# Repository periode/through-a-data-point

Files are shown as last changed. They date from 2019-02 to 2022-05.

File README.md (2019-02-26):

# through-a-data-point
Code + doc for Data Through Design 2019

## HARDWARE

- 4x [Stepper Motor](https://www.sparkfun.com/products/10848)
- 4x [L293D Driver IC](https://www.engineersgarage.com/electronic-components/l293d-motor-driver-ic)
- 1x [Raspberry Pi Model 3B](https://www.raspberrypi.org/products/raspberry-pi-3-model-b/)
- 1x Power Supply DC 12V 0.6A
- 1x [Power Connector](https://ftaelectronics.com/image/cache/catalog/RG6%20Cable%20and%20Connectors/Cat6%20Connectors/2Pcs%20CCTV%20Camera%20UTP%20Power%20DC%20Plug%202.1mm%205.5mm%20Fema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)
- 1x MicroSD Card 16GB

## SETUP

### Get the latest code
- from the pi, run: `wget http://enframed.net/deeds/controller.py`

### Video
- following [this](https://scribles.net/customizing-boot-up-screen-on-raspberry-pi/)
- download the latest video by running `wget http://enframed.net/deeds/legal_landscape.mp4` or `wget http://enframed.net/deeds/legal_portrait.mp4`

### Wiring

The diagram for wiring a **single motor** can be found [here](https://github.com/periode/through-a-data-point/tree/master/resources/single_stepper_diagram.pdf).

Things to take into consideration:
- The power source is represented as 2x AA Batteries. It should instead be the 12V power supply, connected to the [power connector](https://ftaelectronics.com/image/cache/catalog/RG6%20Cable%20and%20Connectors/Cat6%20Connectors/2Pcs%20CCTV%20Camera%20UTP%20Power%20DC%20Plug%202.1mm%205.5mm%20Fema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).
- The wires coming out of the stepper motor are black and red. For clarity, I've connected them to wires that are the same as their actual color (red, green, yellow, blue).
  - This means that red and yellow go on one side of the IC, while green and blue should go on the other side.
  
 #### Tip
 
 Here's a shortcut to finding wire pairs for a bipolar (4 wire) motor. Spin your stepper motor with your fingers. Depending on the size / holding torque this could be easy or pretty hard. All you really want from this is to get a feel how the motor spins without any of the wires connected to each other. Now that you know how hard it is to spin with your fingers, connect 2 wires together, any two. Try to spin the motor again. If it feels the same then these are **NOT** connected to the same coil. Disconnect these wires. Connect one of the other wires to one of the first wire pairs you tried. Try to spin the motors again. This should be **much** harder. If so, you have found your wire pairs. Each pair goes on one side of the L293D.

## Programming

In order to set up the raspberry pi, you will need to **install** it, **find** it, **connect** to it and **execute** the sample program.

1. Download the [disk image](https://drive.google.com/open?id=1BWNo9bP_HmcmEQR-66aUi-tPA5VI7Kre) that we will flash on the SD card.
2. Download [Etcher](https://www.balena.io/etcher/).
3. Insert the SD card in your computer.
4. Open Etcher, select the image you just downloaded and the SD card you just inserted, and flash.
5. Insert the microSD card in the raspberry pi and connect it to a power source. A microUSB plugged in to a laptop is enough.
6. Once the raspberry pi is powered up, you should see a solid blinking LED.

### How to find your IP Address
7. On your computer, open the Command Prompt and type `ping raspberrypi`. The [output](http://j.tlns.be/wp-content/uploads/2015/02/step2_ping.png) should give you the IP address of the raspberry pi. **Make sure you are on the same WiFi network as the raspberry Pi**.
7. Install [Fing](https://play.google.com/store/apps/details?id=com.overlook.android.fing) and scan your wifi network to find connected devices.
7. Insert the SD Card into your computer. A `boot` disk should appear. Inside the boot partition, create a file called `wpa_supplicant.conf`, this is the file which connects automatically to WiFi networks. The file contents should look like [this](https://github.com/periode/through-a-data-point/blob/master/code/wpa_supplicant.conf) (make sure it's the correct ssid/pw for your own wifi!).
7. Plug in the raspberry pi directly to your router. Then open the command prompt and type `arp -a`. Your raspberry pi is the device that starts with the MAC address `b8:27:eb`.

### Connect and run the code
8. Download [Putty](https://www.chiark.greenend.org.uk/~sgtatham/putty/latest.html) (you probably want the 64bit MSI version).
9. Enter the IP address of the raspberry pi in the `Host Name (or IP address)` field, with `Port` set to 22 and click `Open`.
10. A command prompt should open. When asked to login as, enter `pi` and for password enter `raspberry`.
11. You are now connected to the raspberry pi. To execute the code to make the stepper motor turn, type `python stepper.py` and press `ENTER`. Follow the prompts on the screen to select the delays/numbers of rotations.

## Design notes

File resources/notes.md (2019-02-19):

## TODO
- play a video on the raspberry pin (using `subprocess.POpen()` and `omxplayer`)
- write logic for one cycle
- - motors reset (how? manual setup? there should be an ssh connection possible to go and set it up)
- - 0. pick a video
- - 1. the video plays
- - 2. motors go up at a certain number of steps **step number is fixed for all motors** but there is the problem that sometimes the motors don't actually go through all the steps when they are too fast with the shift register... so we will need trial and error to figure out what is a safe number of steps
- - 3. once the numbers have gone up all these steps, we stop the video
- - 4. the motors go down the previous number of steps.
- - 5. go to step 1.

## MOTOR NOTES

for the motors pierre has:
- blue and yellow
- red and green

same coil: same side of the l293d

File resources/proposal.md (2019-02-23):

### Short description of your proposed exhibition
Below, just a point is a light installation which reveals the sensual intersection between data points whose effects are unquantifiable because they’re unavailable and data points whose effects are only too quantifiable, but not searchable.

This installation wants to highlight the cause and effect relationship between property transactions —often happening unbeknownst to and to the detriment of inhabitants— and the amount of sunlight that these inhabitants are exposed to. On a very physical level, property transfer results directly in the construction of ever-higher rises, following a logic of most value extraction from the land, which in turn manifests itself through a net disappearance of sunlight for current tenants and neighbors upon completion of the construction work.

On the one side, then, data quantifying the amount of sunlight that urban zones are exposed to throughout the year is well documented, and visualized using current state-of-the-art technology from both specialized outlets (MAS - Municipal Arts Society), and broadsheet publications (NYT - New York Times); it is the very experience of seeing the light disappear that prevents readers and audience members to truly experience what it meant, not to live in shadows, but to see the light disappear.

On the other side, as the buildings rise, they obfuscate the original act of their creation —the financial exchange of mortgages— as they get buried deeper and deeper into the ACRIS database, supposedly open, yet hardly searchable, hardly findable, only remnants of deeds.

### Proposal submission
Through a data point, darkly consists in three main components. A projector, a set of moveable pieces articulated by DC motors and controlled by a Raspberry Pi, and a set of documents from the ACRIS database being projected. Placed right in front of the projector lens, the moveable pieces slowly rise to the pace at which a given set of buildings is expected to be completed within a neighborhood in New York City, gradually obstructing the light from the projector, casting their shadow on the projected documents, a set of mortgage transactions which have allowed that construction to happen in the first place. As the light gets obstructed from below, the impression is that of these legal documents disappearing. Once the automated, makeshift building silhouette has completely covered the light, the system resets and moves on to another lot, another mortgage, another construction.

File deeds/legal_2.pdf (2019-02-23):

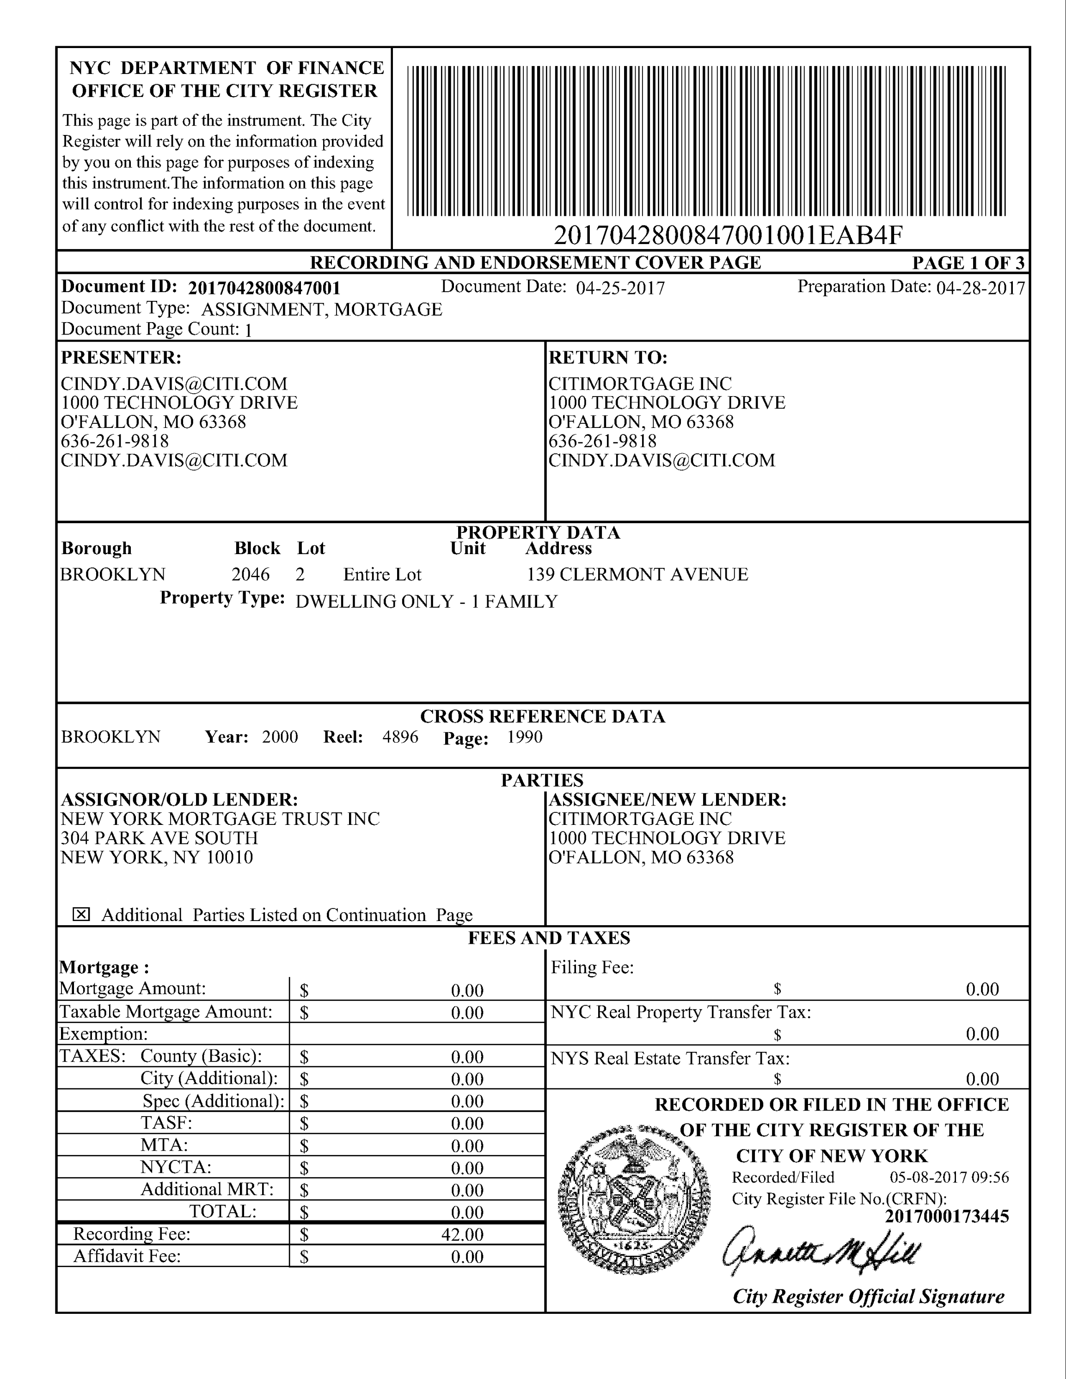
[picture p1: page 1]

Untitled Document | https://a836-acris.nyc.gov/DS/DocumentSearch/DocumentImag...
1 of 3 | 2/22/19, 6:17 PM

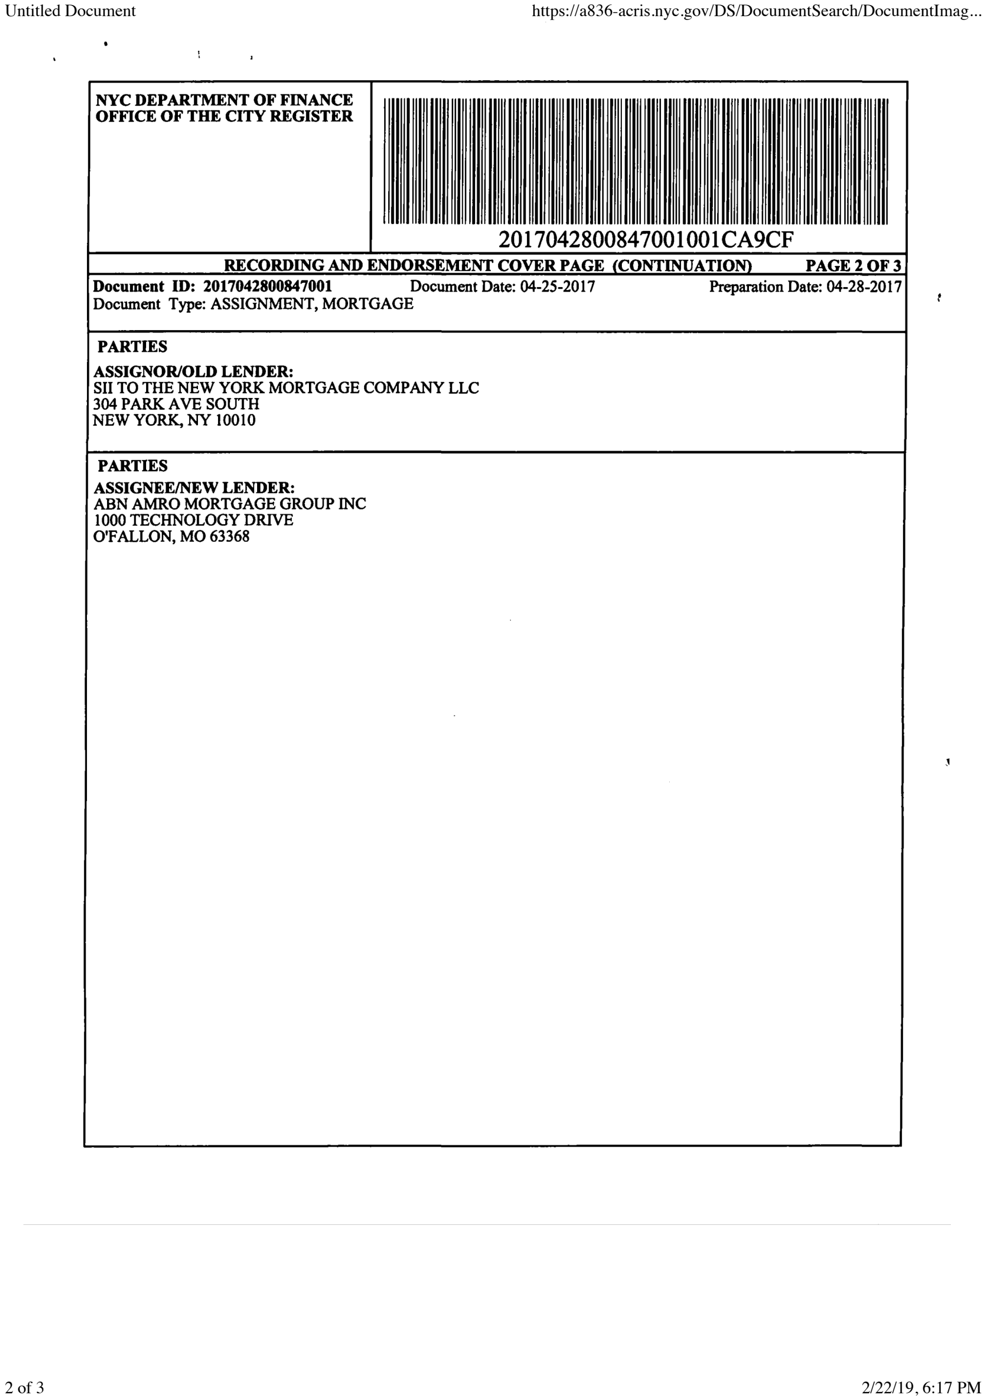
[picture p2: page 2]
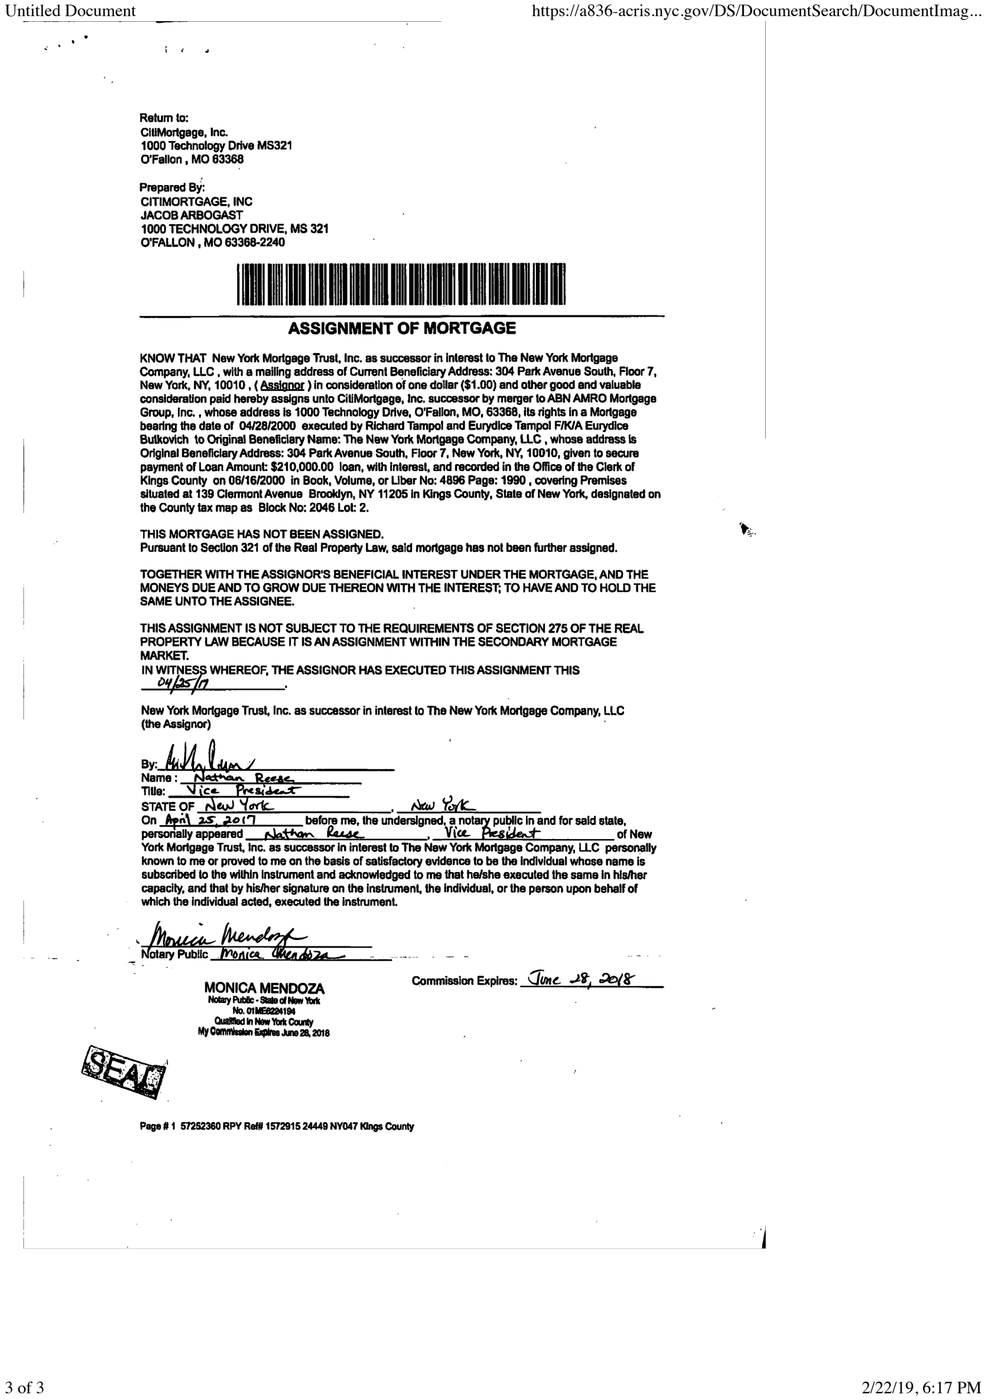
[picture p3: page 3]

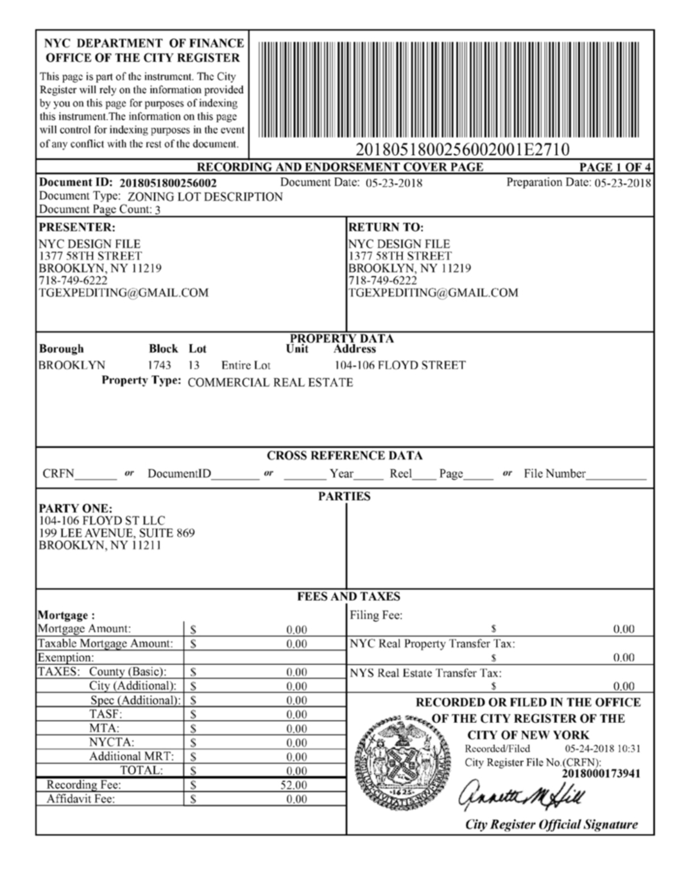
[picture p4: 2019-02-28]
deeds/img/legal_1-10.jpg

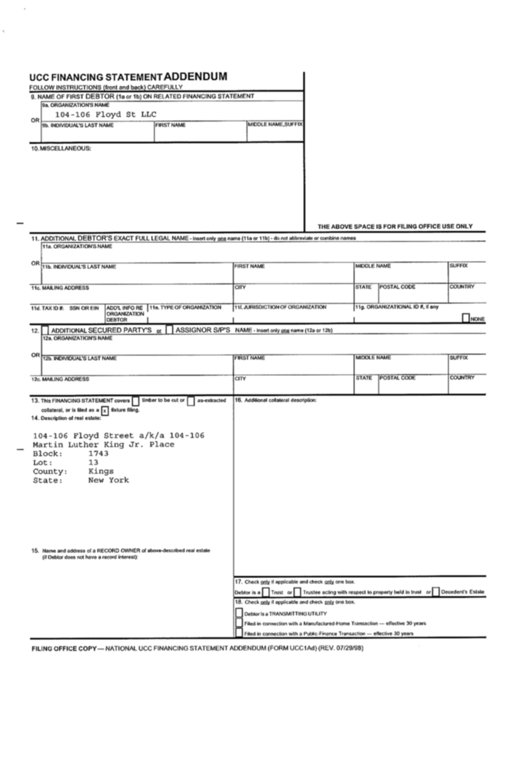
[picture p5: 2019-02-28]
deeds/img/legal_1-2.jpg

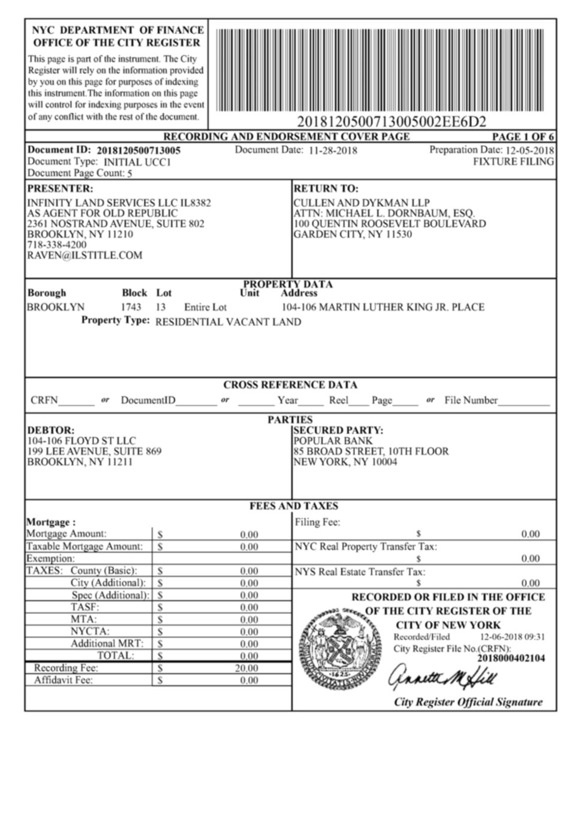
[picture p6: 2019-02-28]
deeds/img/legal_1-0.jpg

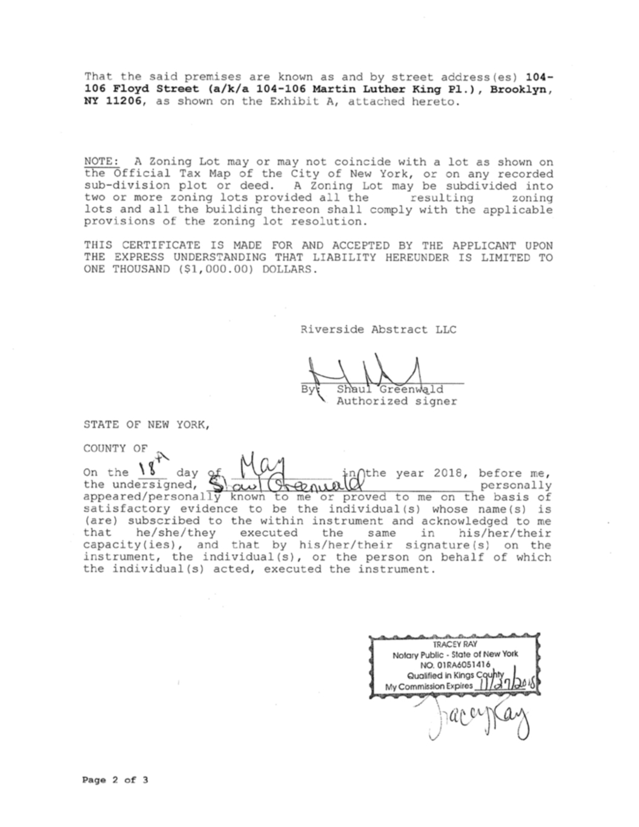
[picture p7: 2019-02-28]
deeds/img/legal_1-8.jpg

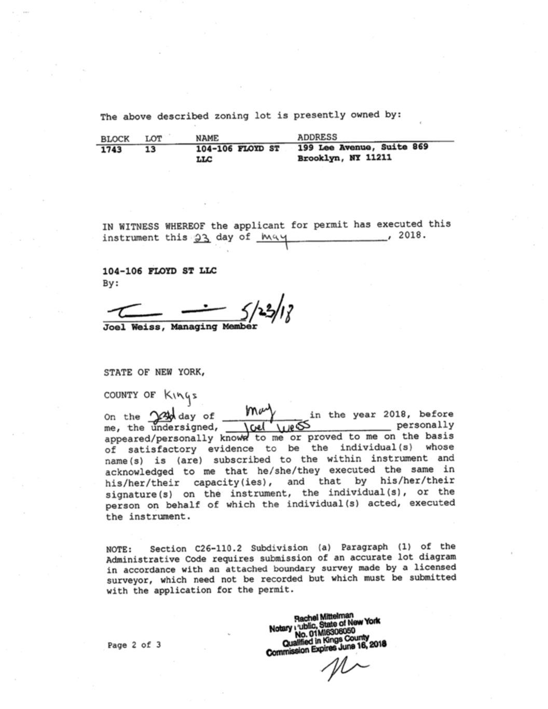
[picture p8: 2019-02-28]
deeds/img/legal_1-12.jpg

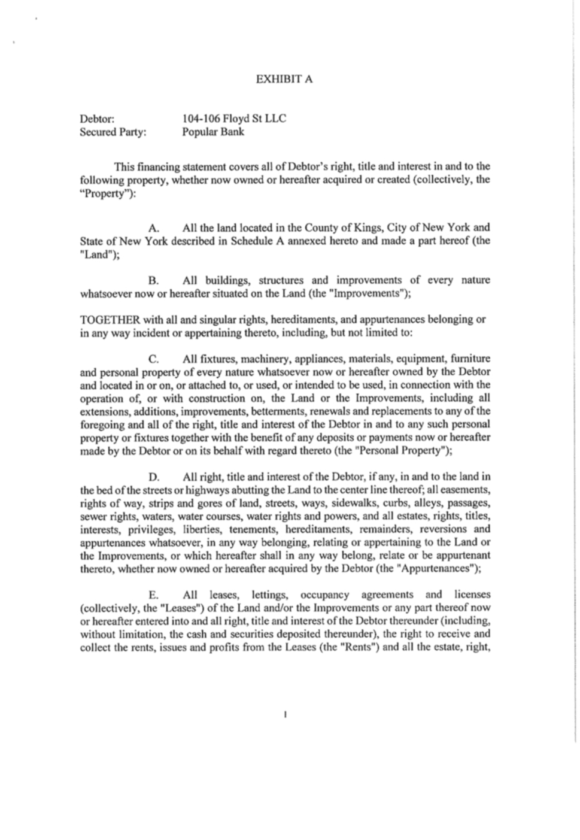
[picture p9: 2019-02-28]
deeds/img/legal_1-3.jpg

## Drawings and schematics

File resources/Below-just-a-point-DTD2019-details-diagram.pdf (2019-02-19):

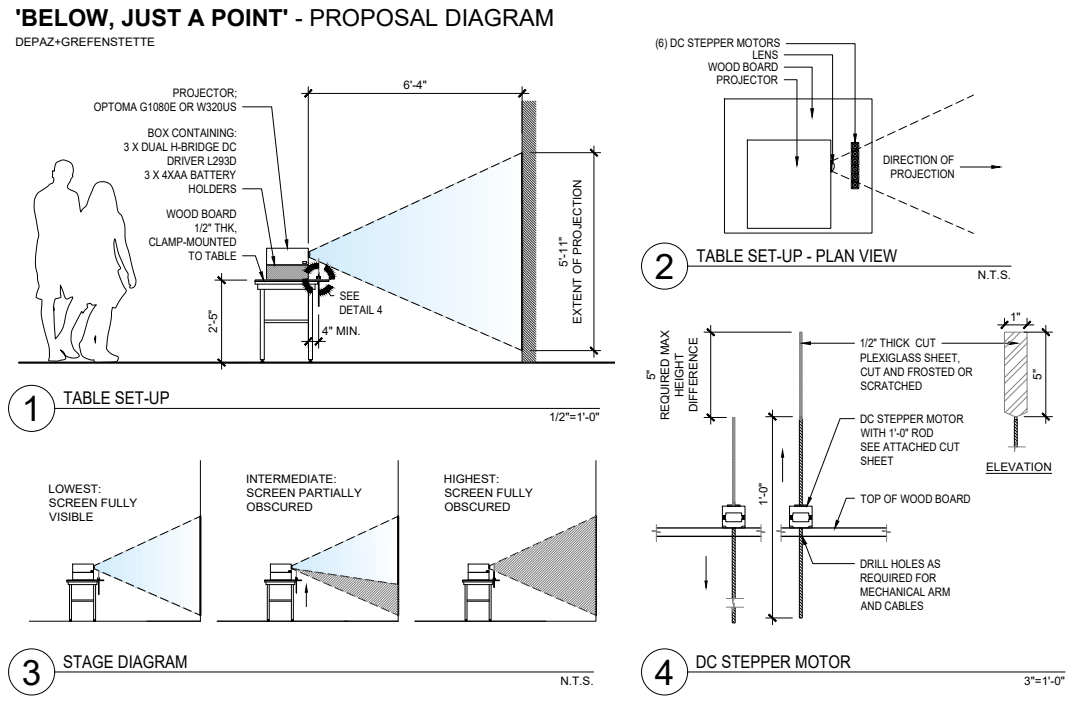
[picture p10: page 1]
REQUIRED MAX

5" ELEVATION TABLE SET-UP 1 1/2"=1'-0" TABLE SET-UP - PLAN VIEW 2 N.T.S. STAGE DIAGRAM 3 N.T.S. DC STEPPER MOTOR 4 3"=1'-0" 'BELOW, JUST A POINT' - PROPOSAL DIAGRAM DEPAZ+GREFENSTETTE

2'-5" LOWEST: SCREEN FULLY VISIBLE INTERMEDIATE: SCREEN PARTIALLY OBSCURED HIGHEST: SCREEN FULLY OBSCURED DIRECTION OF PROJECTION (6) DC STEPPER MOTORS LENS WOOD BOARD PROJECTOR

EXTENT OF PROJECTION 6'-4" 4" MIN. PROJECTOR; OPTOMA G1080E OR W320US BOX CONTAINING: 3 X DUAL H-BRIDGE DC DRIVER L293D 3 X 4XAA BATTERY HOLDERS WOOD BOARD 1/2" THK, CLAMP-MOUNTED TO TABLE SEE DETAIL 4

DIFFERENCE DC STEPPER MOTOR WITH 1'-0" ROD SEE ATTACHED CUT SHEET 1/2" THICK CUT PLEXIGLASS SHEET, CUT AND FROSTED OR SCRATCHED TOP OF WOOD BOARD DRILL HOLES AS REQUIRED FOR MECHANICAL ARM AND CABLES 1"

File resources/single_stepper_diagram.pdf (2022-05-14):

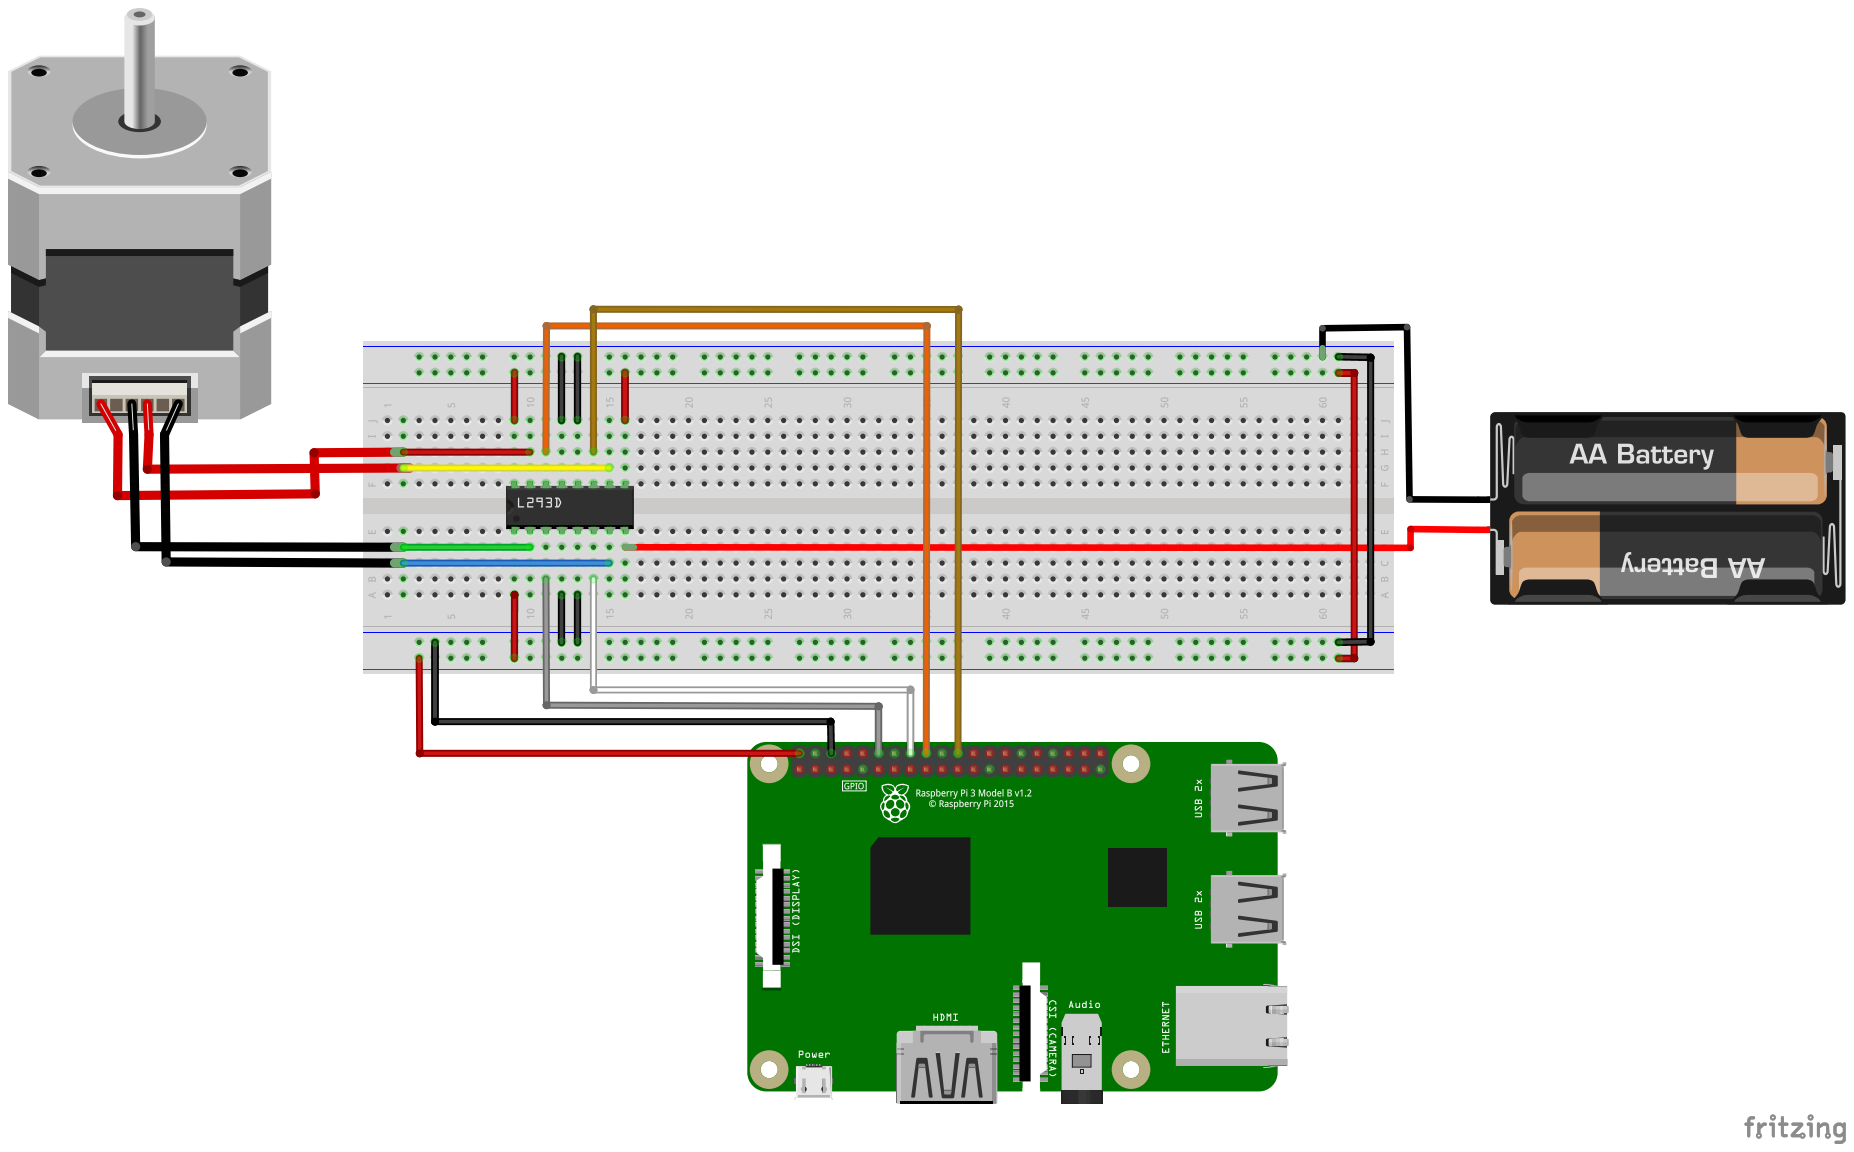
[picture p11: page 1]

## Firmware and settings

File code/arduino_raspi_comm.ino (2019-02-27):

bool isDone = false;
bool isGoingUp = true;

int startTime = 0;
int timer = 1000;

int currentSteps = 0;
int totalSteps = 120;

int delayUp = 25;
int delayDown = 5;

int motor1pinA = 2;
int motor1pinB = 4;
int motor1pinC = 3;
int motor1pinD = 5;

void setup() {

  pinMode(motor1pinA, OUTPUT);
  pinMode(motor1pinB, OUTPUT);
  pinMode(motor1pinC, OUTPUT);
  pinMode(motor1pinD, OUTPUT);
  
  Serial.begin(9600);
}

void loop() {
//  if(millis() - startTime > timer){
//      Serial.println(isDone);
//  
//      isDone = !isDone;
//      startTime = millis();
//  }

  // first we're going up, for up to X steps
  if(currentSteps < totalSteps && isGoingUp){
    up();  
    currentSteps++;
  }else{ //if we've reached the top
    if(isGoingUp){ //we send a signal to the pi
      Serial.println("reached top");
      isGoingUp = false;
    }
    
    down();
    currentSteps--;

    if(currentSteps == 0){ //if we've reached the bottom
      Serial.println("reached bottom");
      isGoingUp = true;
    }
    
  }
  

}

void up(){
  digitalWrite(motor1pinA, HIGH);
  digitalWrite(motor1pinB, LOW);
  digitalWrite(motor1pinC, LOW);
  digitalWrite(motor1pinD, LOW);
  delay(delayUp);
  digitalWrite(motor1pinA, LOW);
  digitalWrite(motor1pinB, HIGH);
  digitalWrite(motor1pinC, LOW);
  digitalWrite(motor1pinD, LOW);
  delay(delayUp);
  digitalWrite(motor1pinA, LOW);
  digitalWrite(motor1pinB, LOW);
  digitalWrite(motor1pinC, HIGH);
  digitalWrite(motor1pinD, LOW);
  delay(delayUp);
  digitalWrite(motor1pinA, LOW);
  digitalWrite(motor1pinB, LOW);
  digitalWrite(motor1pinC, LOW);
  digitalWrite(motor1pinD, HIGH);
  delay(delayUp);
}

void down(){
  digitalWrite(motor1pinA, LOW);
  digitalWrite(motor1pinB, LOW);
  digitalWrite(motor1pinC, LOW);
  digitalWrite(motor1pinD, HIGH);
  delay(delayDown);
  digitalWrite(motor1pinA, LOW);
  digitalWrite(motor1pinB, LOW);
  digitalWrite(motor1pinC, HIGH);
  digitalWrite(motor1pinD, LOW);
  delay(delayDown);
  digitalWrite(motor1pinA, LOW);
  digitalWrite(motor1pinB, HIGH);
  digitalWrite(motor1pinC, LOW);
  digitalWrite(motor1pinD, LOW);
  delay(delayDown); 
  digitalWrite(motor1pinA, HIGH);
  digitalWrite(motor1pinB, LOW);
  digitalWrite(motor1pinC, LOW);
  digitalWrite(motor1pinD, LOW);
  delay(delayDown);
}

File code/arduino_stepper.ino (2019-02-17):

int motorPin1 = 8;
int motorPin2 = 9;
int motorPin3 = 10;
int motorPin4 = 11;
int delayTime = 10;
 
void setup() {
  pinMode(motorPin1, OUTPUT);
  pinMode(motorPin2, OUTPUT);
  pinMode(motorPin3, OUTPUT);
  pinMode(motorPin4, OUTPUT);
}
 
void loop() {
  digitalWrite(motorPin4, HIGH);
  digitalWrite(motorPin3, LOW);
  digitalWrite(motorPin2, LOW);
  digitalWrite(motorPin1, LOW);
  delay(delayTime);
  digitalWrite(motorPin4, LOW);
  digitalWrite(motorPin3, HIGH);
  digitalWrite(motorPin2, LOW);
  digitalWrite(motorPin1, LOW);
  delay(delayTime);
  digitalWrite(motorPin4, LOW);
  digitalWrite(motorPin3, LOW);
  digitalWrite(motorPin2, HIGH);
  digitalWrite(motorPin1, LOW);
  delay(delayTime);
  digitalWrite(motorPin4, LOW);
  digitalWrite(motorPin3, LOW);
  digitalWrite(motorPin2, LOW);
  digitalWrite(motorPin1, HIGH);
  delay(delayTime);
}

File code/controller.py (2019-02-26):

import sys
import RPi.GPIO as GPIO
import time
import threading
from subprocess import Popen

# CONSTANTS
VIDEO_FILE = "legal_landscape.mp4"

GPIO.setmode(GPIO.BCM)

MOTOR_A_A = 18
MOTOR_A_B = 23
MOTOR_A_C = 24
MOTOR_A_D = 25

MOTOR_B_A = 4
MOTOR_B_B = 17
MOTOR_B_C = 27
MOTOR_B_D = 22

MOTOR_C_A = 12
MOTOR_C_B = 16
MOTOR_C_C = 20
MOTOR_C_D = 21

MOTOR_D_A = 6
MOTOR_D_B = 13
MOTOR_D_C = 19
MOTOR_D_D = 26



class Motor:
    def __init__(self, _id, _a, _b, _c, _d):
        self.id = _id
        self.pins = [_a, _b, _c, _d]

    def setStep(self, values):
        GPIO.output(self.pins[0], values[0])
        GPIO.output(self.pins[1], values[1])
        GPIO.output(self.pins[2], values[2])
        GPIO.output(self.pins[3], values[3])

    def up(self, delay, steps):
        for i in range(0, steps):
            self.setStep([1, 0, 1, 0])
            time.sleep(delay)
            self.setStep([0, 1, 1, 0])
            time.sleep(delay)
            self.setStep([0, 1, 0, 1])
            time.sleep(delay)
            self.setStep([1, 0, 0, 1])
            time.sleep(delay)


    def down(self, delay, steps):
        for i in range(0, steps):
            self.setStep([1, 0, 0, 1])
            time.sleep(delay)
            self.setStep([0, 1, 0, 1])
            time.sleep(delay)
            self.setStep([0, 1, 1, 0])
            time.sleep(delay)
            self.setStep([1, 0, 1, 0])
            time.sleep(delay)

    def move(self, dir, delay, steps):
        if dir == "up":
            t = threading.Thread(target=self.up, args=(delay, steps))
            t.start()
        else:
            t = threading.Thread(target=self.down, args=(delay, steps))
            t.start()

    def reset(self):
        self.setStep([0, 0, 0, 0])

motors = []

motors.append(Motor("A", MOTOR_A_A, MOTOR_A_B, MOTOR_A_C, MOTOR_A_D))
motors.append(Motor("B", MOTOR_B_A, MOTOR_B_B, MOTOR_B_C, MOTOR_B_D))
motors.append(Motor("C", MOTOR_C_A, MOTOR_C_B, MOTOR_C_C, MOTOR_C_D))
motors.append(Motor("D", MOTOR_D_A, MOTOR_D_B, MOTOR_D_C, MOTOR_D_D))

GPIO.setup(MOTOR_A_A, GPIO.OUT)
GPIO.setup(MOTOR_A_B, GPIO.OUT)
GPIO.setup(MOTOR_A_C, GPIO.OUT)
GPIO.setup(MOTOR_A_D, GPIO.OUT)

GPIO.setup(MOTOR_B_A, GPIO.OUT)
GPIO.setup(MOTOR_B_B, GPIO.OUT)
GPIO.setup(MOTOR_B_C, GPIO.OUT)
GPIO.setup(MOTOR_B_D, GPIO.OUT)

GPIO.setup(MOTOR_C_A, GPIO.OUT)
GPIO.setup(MOTOR_C_B, GPIO.OUT)
GPIO.setup(MOTOR_C_C, GPIO.OUT)
GPIO.setup(MOTOR_C_D, GPIO.OUT)

GPIO.setup(MOTOR_D_A, GPIO.OUT)
GPIO.setup(MOTOR_D_B, GPIO.OUT)
GPIO.setup(MOTOR_D_C, GPIO.OUT)
GPIO.setup(MOTOR_D_D, GPIO.OUT)


def main():
    try:
        for motor in motors:
            motor.reset()

        Popen(['/usr/bin/omxplayer', VIDEO_FILE])
        motors[0].move("up", 0.075, 40)
        motors[1].move("down", 0.025, 40)
        motors[2].move("down", 0.055, 40)
        motors[3].move("up", 0.085, 40)

        for t in threading.enumerate():
            try:
                t.join()
            except RuntimeError as err:
                if 'cannot join current thread' in err:
                    continue
                else:
                    raise

        GPIO.cleanup()

    except KeyboardInterrupt:
        print "exiting"
        GPIO.cleanup()
    sys.exit(0)

main()

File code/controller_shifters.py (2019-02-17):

import sys
import RPi.GPIO as GPIO
import time
import threading

# NOTES
# threading time

GPIO.setmode(GPIO.BCM)
## 1
CLOCK_1 = 18 #green
DATA_1 = 23 #blue
LATCH_1 = 24 #orange

CLOCK_2 = 6 #orange
DATA_2 = 25 #purple
LATCH_2 = 12 #yellow

CLOCK_3 = 26 #white
DATA_3 = 16 #grey
LATCH_3 = 20 #white

forward_first = [
    10, # 1010,
    6,  # 0110,
    5,  # 0101,
    9   # 1001
]
forward_second = [160, 96, 80, 144]

backward_first = [
    9, # 1001,
    5, # 0101,
    6, # 0110,
    10 # 1010
]
backward_second = [144, 80, 96, 160]

class Motor:
    def __init__(self, _id, _neighbour, _clock, _latch, _data):
        self.id = _id
        self.neighbour = _neighbour
        self.clock_pin = _clock
        self.latch_pin = _latch
        self.data_pin = _data
        if _id == "A" or _id == "C" or _id == "E":
            self.first = True
        else:
            self.first = False

        if(self.first):
            self.fwd = [10, 6, 5, 9]
            self.bwd = [9, 5, 6, 10]
        else:
            self.fwd = [160, 96, 80, 144]
            self.bwd = [144, 80, 96, 160]

    def clock(self):
        GPIO.setmode(GPIO.BCM)
        GPIO.output(self.clock_pin, 1)
        time.sleep(.0001)
        GPIO.output(self.clock_pin, 0)

    def latch(self):
        GPIO.setmode(GPIO.BCM)
        GPIO.output(self.latch_pin, 1)
        time.sleep(.0001)
        GPIO.output(self.latch_pin, 0)

    def writePin(self, value):
        for x in range(0, 8):
            temp = value & 0x80
            if temp == 0x80:
                GPIO.output(self.data_pin, 1)
            else:
                GPIO.output(self.data_pin, 0)
            self.clock()
            value = value << 0x01
        self.latch()

    def up(self, delay, steps):
        GPIO.setmode(GPIO.BCM)
        for i in range(0, steps):
            self.writePin(self.fwd[0])
            time.sleep(delay)
            self.writePin(self.fwd[1])
            time.sleep(delay)
            self.writePin(self.fwd[2])
            time.sleep(delay)
            self.writePin(self.fwd[3])
            
        self.reset()

    def down(self, delay, steps):
        for i in range(0, steps):
            self.writePin(self.bwd[0])
            time.sleep(delay)
            self.writePin(self.bwd[1])
            time.sleep(delay)
            self.writePin(self.bwd[2])
            time.sleep(delay)
            self.writePin(self.bwd[3])
        self.reset()

    def move(self, dir, delay, step):
        if dir == "up":
            t = threading.Thread(target=self.up, args=(delay, step))
            t.start()
        else:
            t = threading.Thread(target=self.down, args=(delay, step))
            t.start()

    def reset(self):
        for state in [0, 0, 0, 0]:
            self.writePin(state)

motors = []

motors.append(Motor("A", "B", CLOCK_1, LATCH_1, DATA_1))
motors.append(Motor("B", "A", CLOCK_1, LATCH_1, DATA_1))
motors.append(Motor("C", "D", CLOCK_2, LATCH_2, DATA_2))
motors.append(Motor("D", "C", CLOCK_2, LATCH_2, DATA_2))
motors.append(Motor("E", "F", CLOCK_3, LATCH_3, DATA_3))
motors.append(Motor("F", "E", CLOCK_3, LATCH_3, DATA_3))

GPIO.setup(CLOCK_1, GPIO.OUT)
GPIO.setup(DATA_1, GPIO.OUT)
GPIO.setup(LATCH_1, GPIO.OUT)

GPIO.setup(CLOCK_2, GPIO.OUT)
GPIO.setup(DATA_2, GPIO.OUT)
GPIO.setup(LATCH_2, GPIO.OUT)

GPIO.setup(CLOCK_3, GPIO.OUT)
GPIO.setup(DATA_3, GPIO.OUT)
GPIO.setup(LATCH_3, GPIO.OUT)

GPIO.output(LATCH_1, 0) #we close the latch
GPIO.output(LATCH_2, 0)
GPIO.output(LATCH_3, 0)
GPIO.output(CLOCK_1, 0) #idk/
GPIO.output(CLOCK_2, 0)
GPIO.output(CLOCK_3, 0)

def main():
    try:
        for motor in motors:
            motor.reset()
        #motors[4].move("up", 0.195, 40)
        motors[5].move("down", 0.175, 40)
        for t in threading.enumerate():
            try:
                t.join()
            except RuntimeError as err:
                if 'cannot join current thread' in err:
                    continue
                else:
                    raise
        GPIO.cleanup()

    except KeyboardInterrupt:
        print "exiting"
        GPIO.cleanup()
    sys.exit(0)

main()

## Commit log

2019-02-09 added resources
    [single_stepper.fzz]
2019-02-19 "updated resources"
    [single_stepper.fzz]
2019-02-23 added controller with 4 motors
2019-02-26 images and fixed fritzing
    [single_stepper.fzz]
2019-02-27 added raspi arduino comm
